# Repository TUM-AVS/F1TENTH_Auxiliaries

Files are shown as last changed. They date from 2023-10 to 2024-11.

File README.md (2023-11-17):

# Table of Contents
- [F1TENTH_Auxiliaries](#f1tenth-auxiliaries)
  * [F1TENTH - Bill of Materials Deutschland/ Germany/ EU](#f1tenth---bill-of-materials-deutschland--germany--eu)
  * [F1TENTH - Bash Scripts](#f1tenth---bash-scripts)
  * [F1TENTH - CAD Files](#f1tenth---cad-files)
  * [TUM - Odometry Files](#tum---odometry-files)

# F1TENTH_Auxiliaries
The F1TENTH_Auxiliaries repository is a collection of essential helper tools and resources created to facilitate the experience of working with F1TENTH autonomous racing cars. More information on F1TENTH, developed by Prof. Rahul Mangharam at the University of Pennsylvania, can be found on the official website: [Official F1TENTH website](f1tenth.org "F1TENTH website").

All elements on this website are developed by [Felix Jahncke](https://www.mos.ed.tum.de/en/avs/team/felix-jahncke/ "Felix Jahncke website"), a Ph.D. student at the Autonomous Vehicle Systems (AVS) Lab, Technical University of Munich (TUM), supervised by Prof. Dr.-Ing. Johannes Betz.: [AVS website](https://www.mos.ed.tum.de/en/avs/home/ "AVS website").

In addition, multiple students developed parts of this repository during their bachelor's, semester's, or master's thesis. Contributions are acknowledged within each specific resource.

For inquiries or further information, please write an email to [felix.jahncke@tum.de](mailto:felix.jahncke@tum.de?subject=F1TENTH%20Auxiliaries%20Repository).

## F1TENTH - Bill of Materials Deutschland/ Germany/ EU
This document contains an Excel file with an adjusted Bill of Materials for Germany. This can also be helpful for other European Countries, avoiding additional workload through taxes and customs. An exception is the VESC, which can only be ordered in the UK. It is indicated for each item whether it can be ordered by invoice. This process is particularly important for accounting at German universities and reduces the need to personally pay the money.

Please note that our mechanical and electrical workshops construct the platform decks and powerboards, which are not included in our Bill of Materials (BOM) at this time.

## F1TENTH - Bash Scripts
> :warning: **Warning**: Currently under construction!

Multiple bash scripts exist to install different elements of the F1TENTH software stack, such as:
- Initial setup and ROS2 installation
- F1TENTH software stack
- ZED camera ROS2 driver

## F1TENTH - CAD Files
We have developed CAD files for specific purposes, including:
- Slash Platform Holder: Mounts improving the robustness and stability of the autonomy platform on the Slack chassis (no need to hot glue the standoffs anymore)
- Camera-LiDAR mount: Mounting a ZED-2 camera above the LiDAR sensor
- U-Stand: Stands to double stack the F1TENTH racetrack boundaries

## TUM - Odometry Files
This section contains tuned odometry files for all TUM F1TENTH cars. The tuning follows the official F1TENTH instructions found here: [F1TENTH Odometry Calibration](https://github.com/f1tenth/f1tenth_doc/blob/foxy_test/getting_started/driving/drive_calib_odom.rst "F1TENTH Odometry Calibration")

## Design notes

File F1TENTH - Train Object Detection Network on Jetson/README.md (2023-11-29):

## Instructions to train an object detection network directly on an NVIDIA Jetson Orin Nano

1. Increase the Swap Size to 16GB according to this repo: [JetsonHacks Swap Size](https://github.com/JetsonHacksNano/resizeSwapMemory "JetsonHacks Swap Size")
2. Install Tensorflow for Jetson for Tensorboard: [Install Tensorflow on Jetson](https://docs.nvidia.com/deeplearning/frameworks/install-tf-jetson-platform/index.html "Install Tensorflow on Jetson")
3. Install PyTorch with CUDA bindings on Jetson: [Install PyTorch on Jetson](https://docs.nvidia.com/deeplearning/frameworks/install-pytorch-jetson-platform/index.html "Install PyTorch on Jetson")
4. Verify the functionality of the install by running the following commands in a terminal:
- "python3"
- "import torch"
- "print(torch.cuda.is_available())"
If the command prints true at the end, Torch can use the GPU.

5. In a terminal: "export LD_PRELOAD=/lib/aarch64-linux-gnu/libGLdispatch.so"
6. python3 train_ssd.py --dataset-type=voc --data=data/cone_dataset --model-dir=models/mobilenetv2 --batch-size=4 --workers=0 --epochs=10
7. python3 onnx_export.py --model-dir=models/mobilenetv2
8. detectnet --model=models/mobilenetv2/ssd-mobilenet.onnx --labels=models/cone_dataset/labels.txt \
          --input-blob=input_0 --output-cvg=scores --output-bbox=boxes \
            /dev/video0

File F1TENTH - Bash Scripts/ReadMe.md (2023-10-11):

# ROS2 and F1Tenth Driver Stack 
## Hokuyu wired connection and udev rules are not edited by the scripts and henced have to be added manually

1. From your home directory run the ros2_installer_script with sudo. 

2. Afterwards again from your home directory run f1tenth_installer_script **but without sudo.** 

_Note: Currently the f1tenth installer stills asks to type in sudo password once, hopefully will fix this in the near future_ 
# ZED2 Installtion of Wrapper adn Examples
## Manually download and install ZED SDK from https://download.stereolabs.com/zedsdk/4.0/l4t35.3/jetsons
Afterwards run the ZED2_installer_script

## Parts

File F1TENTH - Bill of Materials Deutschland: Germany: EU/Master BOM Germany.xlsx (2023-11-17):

Scroll right to see links | Qty | Cost per Unit | Comments | Payable by invoice | Link
Chassis
Traxxas Slash 4x4 1/10 Scale Brushless | 1 | 429.95 € |  | yes | https://www.monsterhopups.de/Traxxas-TRX68086-4-Slash-1/10-4x4-Brushless-TQi-mit-Stabilitaetskontrolle-TSM
2 Lipos and Charger Combo | 1 | 249.95 € |  | yes | https://www.monsterhopups.de/Traxxas-TRX2990GX-POWER-PACK-Dual-EZ-Peak-Plus-Ladegeraet-2x-ID-LiPo-111V-5000mah-25C
Fasteners
Standoff M3 SW6 45mm | 3 | 36.51 € | pack of 100 for Autonomy Platform | yes | https://abstandsbolzen-shop.de/abstandsbolzen/stahl/innen-innengewinde/16/stahl-abstandsbolzen-i/i-gewinde-m3-sw-6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
Standoff M3 SW6 25mm | 3 | 21.60 € | pack of 100 for Powerboard | yes | https://abstandsbolzen-shop.de/abstandsbolzen/stahl/innen-innengewinde/16/stahl-abstandsbolzen-i/i-gewinde-m3-sw-6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
Standoff M3 SW6 20mm | 4 | 21.07 € | pack of 100 for Jetson | yes | https://abstandsbolzen-shop.de/abstandsbolzen/stahl/innen-innengewinde/16/stahl-abstandsbolzen-i/i-gewinde-m3-sw-6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
Screws M3x14mm | 10 | 2.14 € | pack of 100 3x for Autonomy Platform 4x for Jetson bottom 3x for Powerboard bottom | yes | https://www.conrad.de/de/p/iso4762-din912-m3x14-zylinderschrauben-mit-innensechskant-vollgewinde-material-a2-blank-100-stueck-865439039.html
Screws M3x8mm | 9 | 28.99 € | pack of 100 4x for Jetson top 3x for Powerboard op 2x for ZED 2 | yes | https://www.conrad.de/de/p/toolcraft-888123-zylinderschrauben-m3-8-mm-sechsrund-iso-14579-stahl-verzinkt-100-st-888123.html
Screws M3x20mm | 2 | 3.63 € | pack of 100 2x for LiDAR-Camera mount | yes | https://www.conrad.de/de/p/iso4017-din933-m3x20-sechskantschraube-gewinde-bis-kopf-vollgewinde-material-a2-blank-100-stueck-865407903.html
Screws M5x | 2 | 6.37 € | pack of 100 2x for VESC | yes | https://www.conrad.de/de/p/zylinderschraube-din-912-innen-6kt-m5x20-8-8-galv-verz-100st-806478117.html
Compute module
Jetson Orin Nano Developer Kit | 1 | 617.61 € |  | yes | https://de.rs-online.com/web/p/entwicklungstools-prozessor/2647384
Micro SD Card 128 GB | 1 | 15.99 € |  | yes | https://www.conrad.de/de/p/sandisk-extreme-microsdxc-karte-128-gb-class-10-uhs-i-stosssicher-wasserdicht-2621014.html
NVMe SSD Card 1TB | 1 | 97.81 € |  | yes | https://www.conrad.de/de/p/samsung-970-evo-plus-1-tb-interne-m-2-pcie-nvme-ssd-2280-m-2-nvme-pcie-3-0-x4-retail-mz-v7s1t0bw-1910197.html
Wifi Antenna | 1 | 29.99 € | Optional, since Jetson has a not so good internal Bluetooth and Wifi module quite fragile,currently looking for an alternative | yes | https://www.conrad.de/de/p/edimax-ew-7811uac-wlan-stick-usb-2-0-433-mbit-s-1188098.html
Bluetooth Adapter | 1 | 14.90 € | see above | yes | https://www.conrad.de/de/p/asus-usb-bt500-bluetooth-stick-5-0-2336738.html
Sensors
ZED 2 camera (optional) | 1 | 449.00 € |  | no | https://store.stereolabs.com/en-de/products/zed-2
Hokuyo 10LX | 1 | 1606.50 € |  | yes | https://www.roboparts.de/epages/63257595.sf/sec37340fc51c/?ObjectPath=/Shops/63257595/Products/UST-10LX
Electronics
VESC 6 MkVI | 1 | 413.62 € | incl. Bluetooth module for easier parameter tuning and dust cover incl. Customs fees | no | https://trampaboards.com/vesc-6-mkvi-the-amazing-trampa-vesc-6-mkvi--gives-maximum-power-original-p-27536.html
Dualshock 5 for PS5 | 1 | 76.21 € |  | yes | https://www.conrad.de/de/p/sony-dualsense-wireless-controller-midnight-black-gamepad-playstation-5-schwarz-2386057.html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
USB A to USB micro cable | 1 | 3.99 € |  | yes | https://www.conrad.de/de/p/renkforce-usb-kabel-usb-2-0-usb-a-stecker-usb-micro-b-stecker-0-30-m-schwarz-vergoldete-steckkontakte-rf-4463076-1487692.html
Cable to connect the battery with the VESC and powerboard | 1 | 24.99 € |  | yes | https://www.monsterhopups.de/Traxxas-TRX2938XX-2938X-ID-Ladekabel-LiPo-Akku-auf-Balancer-Board-2S-bis-4S-XH
4mm male to 3,5mm female bullet adapter for VESC to motor connection | 1 | 7.98 |  | no | https://www.ebay.de/itm/195564348829
Powercord Jetson | 1 | 1.99 € |  | yes | https://www.conrad.de/de/p/tru-components-tc-9556652-niedervolt-anschlusskabel-niedervolt-stecker-offene-kabelenden-5-5-mm-2-5-mm-2-00-m-1-st-2389163.html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
Shrink tube for Servo cable | 1 | 6.95 € |  | yes | https://www.conrad.de/de/p/toolland-has07-schrumpfschlauchsortiment-schwarz-1-set-2574855.html
PPM cable for VESC 6 | 1 | 4.99 € |  | yes | https://shop.elektro-skateboard.de/eigenbau-tuning/esc-motorregler/vesc/747/ppm-kabel-fuer-vesc-6-esc
Miscellaneous
LiPo safety bag like the Aketek Silver Large Size Lipo Battery Guard Sleeve/Bag for Charge & Storage. | 1 | 8.98 € |  | yes | https://www.conrad.de/de/p/extron-modellbau-lipo-safety-bag-1-st-x6670-1930097.html
RC Car Stand | 1 | 24.95 € |  | yes | https://www.conrad.de/de/p/absima-1-10-1-8-montagestaender-schwarz-1537809.html
DisplayPort Dummy | 1 | 8.92 € |  | yes | https://www.conrad.de/de/p/dp-displayport-dummy-plug-displayport-dummy1-818237411.html
Wire ferrules for LiDAR cables | 1 | 29.99 € | set | yes | https://www.conrad.de/de/p/quadrios-2005ca001-aderendhuelsen-sortiment-teilisoliert-mehrfarbig-1200-st-2452883.html
XT90 plug female for power connection VESC | 1 | 1.99 € |  | yes | https://www.conrad.de/de/p/reely-re-6702315-akku-buchse-xt90-vergoldet-1-st-2234105.html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
 | Total: | 4273.65 € | (estimated)
Updated: 2023-11-16
all prices incl. 19% German federal tax

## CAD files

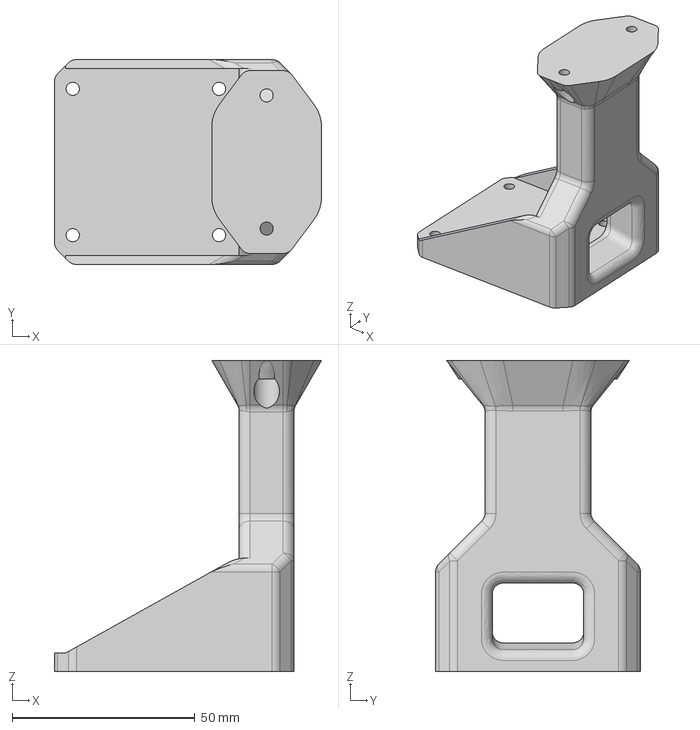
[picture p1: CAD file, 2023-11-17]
F1TENTH - CAD Files/Camera-LiDAR mount/CameraMount_v2.step
73.0 x 56.0 x 85.0 mm

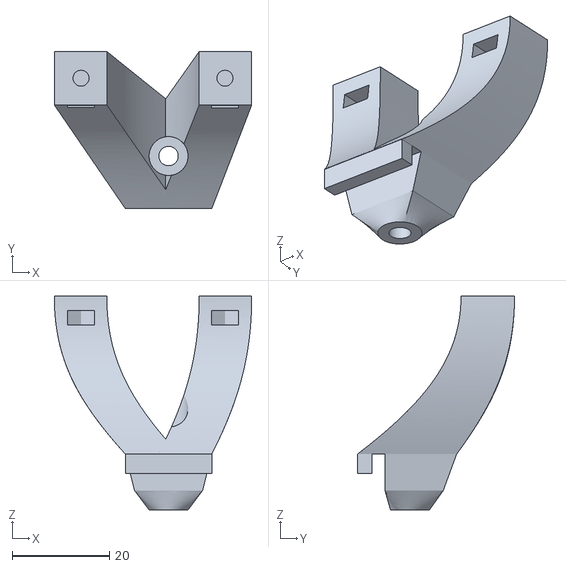
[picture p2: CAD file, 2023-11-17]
F1TENTH - CAD Files/Slash Platform Holder/PlatformMount_opt_v2.stl
40.6 x 32.3 x 44.0

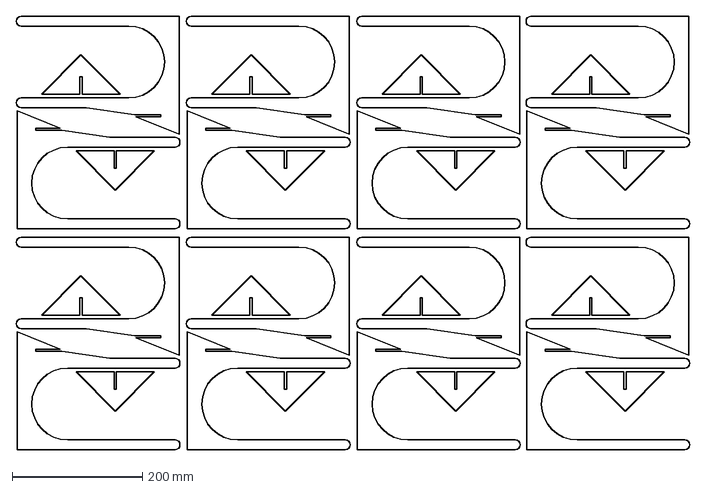
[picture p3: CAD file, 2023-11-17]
F1TENTH - CAD Files/U-Stand/U-Stand.dxf
1033.4 x 664.8 mm

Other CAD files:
F1TENTH - CAD Files/Slash Platform Holder/PlatformMounts_opt_v2.step
F1TENTH - CAD Files/Camera-LiDAR mount/CameraMount_v2.ipt
F1TENTH - CAD Files/Camera-LiDAR mount/CameraMount_v2.stl
F1TENTH - CAD Files/Slash Platform Holder/PlatformMounts_opt_v2.ipt
F1TENTH - CAD Files/U-Stand/U-Stand.dwg

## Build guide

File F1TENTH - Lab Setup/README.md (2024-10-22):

# Instructions to set up an NVIDIA Jetson Orin Nano for all TUM F1TENTH Labs using an SD Card or SSD.
The following instructions where tested and verifies on the following hard- and software on the 31. Jan 2024
- Jetson Orin Nano 8GB Development Kit
- Jetpack 5.1.2
- SD Card (SanDisk Extreme 128GB) and SSD
- ZED 1/2 camera
- Hokuyo UST-10LX
- Hint: Do not use SD Cards if you use the Jetson intensively. It is prone to have corrupted files after some time that can break the entire system.

## General Setup
0. If you want to resetup and SD Card, save all important data from the previous SD Card image.
1. Flash an SD Card with the correct Jetpack Version (currently 5.1.2 [Jetpack 5.1.2 Download](https://developer.nvidia.com/embedded/jetpack-sdk-512)) using, e.g., Balena Etcher: [Balena Etcher Download](https://etcher.balena.io).
2. Insert the SD Card, power up the Jetson and set up the user (username: f1tenth, password: f1tenth).
3. Alternative flash the SSD with the SDK Manager from NVidia: [NVidia SDK Manager](https://developer.nvidia.com/sdk-manager)
4. Update and Upgrade the software:
```
sudo apt-get update && sudo apt-get upgrade
```
5. Install the Wifi driver according to the installation instructions

Clone the repository:
```
git clone https://github.com/RinCat/RTL88x2BU-Linux-Driver.git
```
Navigate inside the directory and build the module:
```
cd RTL88x2BU-Linux-Driver && make clean && make && sudo make install
```
6. Insert the Bluetooth Adapter and Wifi Adapter and check successful connections
7. For usage at TUM in the eduroam Wifi, please log into Eduroam using the official python script you can download [here](https://cat.eduroam.org)
8. Install X11VNC
```
sudo apt-get install x11vnc
```
9. Set the X11 password to f1tenth and save it at the default location
```
x11vnc -storepasswd
```

## Install ROS with the base F1TENTH software stack
1. [Install ROS](https://docs.ros.org/en/foxy/Installation.html)
2. [Install the F1TENTH stack](https://f1tenth.readthedocs.io/en/foxy_test/getting_started/firmware/drive_workspace.html#doc-drive-workspace). Use "rosdep update --include-eol-distros"!

> [!IMPORTANT]  
> The udev files (e.g., /etc/udev/rules.d/99-hokuyo.rules) do not exist yet. Running
> ```
> sudo nano /etc/udev/rules.d/99-hokuyo.rules
> ```
> will create the corresponding file.

3. Add two lines to the bashrc file so no car communicates with each other over Wifi and ROS2 Foxy is automatically sourced.
Open the bash script with:
```
sudo nano ~/.bashrc
```
Enter the following commands after the last line, save and then close the file
```
export ROS_LOCALHOST_ONLY=1
export /opt/ros/foxy/setup.bash
```
4. [Install Zerotier](https://www.zerotier.com/download/) and add the car to the correct network by replacing <network_id> with the corresponding parameter
```
curl -s https://install.zerotier.com | sudo bash
sudo zerotier-cli join <network_id>
```
5. Add a second Ethernet profile called "Standard" with default settings.

## Install the required Packages for Deep Learning
1. Install the corresponding ZED SDK from here: [ZED SDK Download](https://www.stereolabs.com/developers/release). The installation instructions are here: [ZED SDK Installation Instructions](https://www.stereolabs.com/docs/installation/jetson)). Enter yes to all options until it wants to download the AI modules. Enter no there.
```
pip3 install onnx
cd Downloads && chmod +x ZED_SDK* && ./ZED_SDK*
```
2. Add the ZED ROS2 Wrapper to the "f1tenth_ws" workspace and install according to the official repository: [ZED ROS2 Wrapper Installation Instructions](https://github.com/stereolabs/zed-ros2-wrapper)
```
cd ~/f1tenth_ws/src/
git clone  --recursive https://github.com/stereolabs/zed-ros2-wrapper.git
cd ..
sudo apt update
rosdep install --from-paths src --ignore-src -r -y
colcon build --symlink-install --cmake-args=-DCMAKE_BUILD_TYPE=Release --parallel-workers $(nproc)
```
Test the ZED2 Wrapper via:
```
ros2 launch zed_wrapper zed_camera.launch.py camera_model:=<camera_model>
```
Replace <camera_model> with the model of the camera that you are using: 'zed', 'zedm', 'zed2', 'zed2i', 'zedx', 'zedxm'.

3. Increase the Swap Size to 16GB according to this repo: [JetsonHacks Swap Size](https://github.com/JetsonHacksNano/resizeSwapMemory "JetsonHacks Swap Size")
```
sudo nano /etc/systemd/nvzramconfig.sh
```
Change the line:
```
mem=$((("${totalmem}" / 2 / "${NRDEVICES}") * 1024))
```
to:
```
mem=$((("${totalmem}" / "${NRDEVICES}") * 1024 * 2))
```

4. Install Tensorflow for Jetson for Tensorboard: [Install Tensorflow on Jetson](https://docs.nvidia.com/deeplearning/frameworks/install-tf-jetson-platform/index.html "Install Tensorflow on Jetson")
```
sudo apt-get update
sudo apt-get install libhdf5-serial-dev hdf5-tools libhdf5-dev zlib1g-dev zip libjpeg8-dev liblapack-dev libblas-dev gfortran
sudo apt-get install python3-pip
sudo python3 -m pip install --upgrade pip
sudo pip3 install -U testresources setuptools==65.5.0
sudo pip3 install -U numpy==1.22 future==0.18.2 mock==3.0.5 keras_preprocessing==1.1.2 keras_applications==1.0.8 gast==0.4.0 protobuf pybind11 pkgconfig packaging h5py==3.7.0
sudo pip3 install --extra-index-url https://developer.download.nvidia.com/compute/redist/jp/v512 tensorflow==2.12.0+nv23.06
```
5. Install PyTorch with CUDA bindings on Jetson: [Install PyTorch on Jetson](https://docs.nvidia.com/deeplearning/frameworks/install-pytorch-jetson-platform/index.html "Install PyTorch on Jetson")
Download the PyTorch wheel from this link: [Download PyTorch wheel](https://forums.developer.nvidia.com/t/pytorch-for-jetson/72048)
Replace <path/to/torch> with the full path including /home/etc. to the wheel file
```
sudo apt-get -y update;
sudo apt-get -y install python3-pip libopenblas-dev
export TORCH_INSTALL=<path/to/torch>
python3 -m pip install --upgrade pip
python3 -m pip install numpy==1.22
python3 -m pip install --no-cache $TORCH_INSTALL
```
6. Verify the functionality of the install by running the following commands in a terminal
```
python3
import torch
print(torch.cuda.is_available())
exit()
```
If the command prints true at the end, Torch can use the GPU.

7. Install Torchvision with [Install Torchvision on Jetson](https://forums.developer.nvidia.com/t/pytorch-for-jetson/72048)
Look up the torchvision version corresponding to the PyTorch Version
and insert it as e.g. v0.16.1 in <version> and 0.16.1 for <build_version>. The installation takes quite some time.
```
sudo apt-get install libjpeg-dev zlib1g-dev libpython3-dev libopenblas-dev libavcodec-dev libavformat-dev libswscale-dev
git clone --branch <version> https://github.com/pytorch/vision torchvision
cd torchvision
export BUILD_VERSION=<build_version>
python3 setup.py install --user
cd
```
Test via:
```
python3
import torchvision
exit()
```

## Install Jetson Inference for Object Detection Training and Inference on the Jetson
1. Install the Repository:
```
sudo apt-get update
sudo apt-get install git cmake libpython3-dev python3-numpy
git clone --recursive --depth=1 https://github.com/dusty-nv/jetson-inference
cd jetson-inference
mkdir build
cd build
cmake ../
make -j$(nproc)
sudo make install
sudo ldconfig
```
2. Export the Path:
```
export LD_PRELOAD=/lib/aarch64-linux-gnu/libGLdispatch.so
```
3. Test the Inference after plugging in the ZED camera into a USB port:
```
cd jetson-inference/build/aarch64/bin
./detectnet /dev/video0
```
4. Test Model Training:
```
cd jetson-inference/python/training/classification/data
wget https://nvidia.box.com/shared/static/o577zd8yp3lmxf5zhm38svrbrv45am3y.gz -O cat_dog.tar.gz
tar xvzf cat_dog.tar.gz
cd jetson-inference/python/training/classification
python3 train.py --model-dir=models/cat_dog data/cat_dog
python3 onnx_export.py --model-dir=models/cat_dog
NET=models/cat_dog
DATASET=data/cat_dog
imagenet --model=$NET/resnet18.onnx --input_blob=input_0 --output_blob=output_0 --labels=$DATASET/labels.txt $DATASET/test/cat/01.jpg cat.jpg
```
5. Install the Jetson Inference ROS Wrapper
```
cd f1tenth_ws/src
sudo apt-get install ros-foxy-vision-msgs
git clone https://github.com/dusty-nv/ros_deep_learning
cd ..
colcon build
```
Test via:
```
source install/setup.bash
ros2 launch ros_deep_learning detectnet.ros2.launch input:=v4l2:///dev/video0 output:=display://0
```

## Install Range_Libc for the Particle Filter
```
sudo pip3 install cython transforms3d
git clone https://github.com/f1tenth/range_libc.git
cd range_libc
mkdir build
cd build
cmake ..
make
cd ~/range_libc/pywrapper
sudo WITH_CUDA=ON python3 setup.py install #for python3.8
```

## F1TENTH_Waterloo Workspace
```
git clone https://github.com/fjahncke/f1tenth_ws_waterloo.git
sudo apt install ros-foxy-tf-transformations ros-foxy-navigation2
cd f1tenth_ws_waterloo
colcon build --symlink-install
source install/setup.bash
export PYTHONPATH=${PYTHONPATH}:/usr/lib/python3.8/site-packages/range_libc-0.1-py3.8-linux-aarch64.egg
colcon build --symlink-install
```
Test the particle filter:
```
cd f1tenth_ws_waterloo
source install/setup.bash
ros2 launch particle_filter localize_launch.py
```
Test the Pure pursuit node in another terminal at the same time:
```
cd f1tenth_ws_waterloo
source install/setup.bash
ros2 launch pure_pursuit pure_pursuit_launch.py
```

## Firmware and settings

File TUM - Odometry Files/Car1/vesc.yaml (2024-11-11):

/**:
  # general parameters shared by all vesc-related nodes
  ros__parameters:
    # erpm (electrical rpm) = speed_to_erpm_gain * speed (meters / second) + speed_to_erpm_offset
    speed_to_erpm_gain: 4244.0
    speed_to_erpm_offset: 0.0

    # servo value (0 to 1) =  steering_angle_to_servo_gain * steering angle (radians) + steering_angle_to_servo_offset
    steering_angle_to_servo_gain: -0.9485
    steering_angle_to_servo_offset: 0.43504

    port: /dev/sensors/vesc
    duty_cycle_min: 0.0
    duty_cycle_max: 0.0
    current_min: 0.0
    current_max: 100.0
    brake_min: -20000.0
    brake_max: 200000.0
    speed_min: -23250.0
    speed_max: 23250.0
    position_min: 0.0
    position_max: 0.0
    servo_min: 0.125
    servo_max: 0.85

# No longer needed, all parameters are shared
# ackermann_to_vesc_node:
#   ros__parameters:

vesc_to_odom_node:
  ros__parameters:
    odom_frame: odom
    base_frame: base_link
    # publish odom to base link tf
    publish_tf: true
    use_servo_cmd_to_calc_angular_velocity: true
    # car wheelbase is about 25cm
    wheelbase: .25

# No longer needed, all parameters are shared
# vesc_driver:
#   ros__parameters:

throttle_interpolator:
  ros__parameters:
    rpm_input_topic: commands/motor/unsmoothed_speed
    rpm_output_topic: commands/motor/speed
    servo_input_topic: commands/servo/unsmoothed_position
    servo_output_topic: commands/servo/position

    # servo smoother - limits acceleration and smooths anything above limit
    max_acceleration: 2.5 # meters/second^2
    throttle_smoother_rate: 75.0 # messages/sec
    # servo smoother - limits rotation speed and smooths anything above limit
    max_servo_speed: 3.2 # radians/second
    servo_smoother_rate: 75.0 # messages/sec

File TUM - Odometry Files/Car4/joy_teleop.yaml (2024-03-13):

joy:
  ros__parameters:
    # device_name: /dev/input/joypad-f710
    device_id: 0
    deadzone: 0.01
    autorepeat_rate: 20.0
    coalesce_interval: 0.01

joy_teleop:
  ros__parameters:
    default:
      type: topic
      interface_type: ackermann_msgs/msg/AckermannDriveStamped
      topic_name: teleop
      axis_mappings:
        drive-speed:
          axis: 1
          scale: 0.0
          offset: 0.0
        drive-steering_angle:
          axis: 2
          scale: 0.0
          offset: 0.0

    human_control:
      type: topic
      interface_type: ackermann_msgs/msg/AckermannDriveStamped
      topic_name: teleop
      deadman_buttons: [4]
      axis_mappings:
        drive-speed:
          axis: 1
          scale: 6.4
          offset: 0.0
        drive-steering_angle:
          axis: 2
          scale: 0.34
          offset: 0.0

    autonomous_control:
      type: topic
      interface_type: std_msgs/msg/Int8
      topic_name: /dev/null
      deadman_buttons: [5]
      message_value:
        data:
          value: 0

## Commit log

2023-11-16 Update README.md
    Add Bash Script Description and Odometry Files
2023-11-16 Update README.md
    Update regarding powerboard and platform deck
2023-11-16 Update README.md
    CAD files
2023-11-17 CAD Files and BOM Initial Push
    [CameraMount_v2.ipt, CameraMount_v2.step, CameraMount_v2.stl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]
2023-11-17 Folder name adjustment
    [vesc.yaml]
2023-11-17 Updated BOM with Screws
    [Master BOM Germany.xlsx]
2024-01-31 Better visualisation of installation process for the Jetson Inference package, Range_Libc, F1TENTH Waterloo workspace
2024-01-31 Add Jetson Inference ROS
2024-01-31 Install dependency Jetson Inference ROS2 Wrapper
2024-03-13 Odom Files Geradziehen
    [vesc.yaml]
2024-11-11 Added odometry file for vehicle 1 after new setup
    [vesc.yaml]
